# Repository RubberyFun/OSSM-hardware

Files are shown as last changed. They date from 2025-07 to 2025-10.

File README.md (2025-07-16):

# OSSM - Open Source Sex Machine

OSSM Overview Image

### [**KinkyMakers Discord Community**](https://discord.gg/wrENMKb3) 
  
Most OSSM development takes place through ideas and CAD contributions made by enthusiastic discord members, join the discussion or show off your build!  

### Check out our docs at [GitBook](https://kinky-makers.gitbook.io/)

### [**Read the Frequently Asked Questions**](FAQ.md)

## **Summary**   
**OSSM** (pronounced like "awesome") is a user friendly every day sex machine for the people.

The OSSM's primary feature is that it is a servo powered belt-driven linear rail.  
This allows for quiet, high torque operation at speeds up to 1 meter per second, as well as for software-defined stroke and depth. 

**Standard Recommended Build at a glance**
 - 32 lbs (14 kg) of force @ 20v DC
   - Up to 50 lbs (22 kg) @ 36v DC
 - 8" Stroke (20 cm) with 350mm rail

This project aims to help people curious about sex machines explore their interest.   
A second objective is optionally learning how mechanics, electronics, physics and computing are involved in your sexual pleasure.

### **Primary** Design Goals
- Compact & quiet
- Highly performant
- Moderate cost
- 3D printable
- Easily-sourced components
- Moddable
  
<p align="center">

</p>

Note: This is a _work in progress_ and we have attempted to keep compatibility with the current BOM going
forward, but it's not guaranteed.

### Is it *actually* Open Source?
    CERN Open Hardware Licence Version 2 - Strongly Reciprocal
It is one of a kind Certified, Actual, Factual, Open Source  
[](https://certification.oshwa.org/ca000057.html)

Contributions to this GitHub repository assume the same license.

## **Safety**

The safety of the OSSM is yet to be fully characterized as it is a work in progress.  
The OSSM is a framework for building your own sex machine and as such your specific combination may have risks not inherent to other builds.  
**These risks may be undocumented or undiscovered. Please see the [Hazards](Documentation/Hazards.md) file for more information.**

Use of experimental/modified code increases the level of risk.

While using the OSSM we can suggest the following hierarchy of safety, however it is up to you and your build to decide
what risks exist and how to mitigate them.

1. Have ability to move away
2. Have ability to remove the power
3. If you are in bondage, safety is responsibility of the Top

## **Building Your OSSM**
### Motor Support  
 - 57AIM30 "Gold Motor" (Standard Recommended)
 - 42AIM30 "Round Motor" (Smaller form factor, limited mounting support)
 - iHSV57 "Legacy Motor" (Pre-2024 recommended motor)

The OSSM Software is written to support closed loop servo type motors and tested on the above motors.  
Most OSSM actuator and mounting hardware is designed for NEMA23 form factor motors.  
Attempting to use a stepper or other motor is not recommended; while it may be technically possible in some cases, this usually requires custom design work and advanced-level custom code. 

### Bill Of Materials for Standard Recommended Build

### Electronics  

 - Motor 
   - 57AIM30 ["Gold Motor"](https://www.researchanddesire.com/products/ossm-motor-gold-motor)
     - **Important note:** In order to operate with OSSM Software, motors must receive programming to set their "steps per revolution" to 800.
     - Motors from R+D are pre-programmed for OSSM. Motors from all other sources will need programming.
     - Programming requires a USB to 4 pin RS485 connector, cable for the 8 pin white motor plug, and use of the [Gold Motor Programming Tool](/Hardware/Servo%20Tools/Gold%20Motor/)
 - OSSM Reference Board, Remote, Wiring
    - [OSSM Reference PCB](https://www.researchanddesire.com/products/ossm-reference-board) or ESP32 Development Board
      - More information for board development [here](/Documentation/Board_Design.md).
    - [OSSM Remote](https://www.researchanddesire.com/products/ossm-reference-board)
    - JST-PH 2.0 4-Pin data cable and 16awg power wire
      - [Wire harness - Gold Motor](https://www.researchanddesire.com/products/ossm-wire-harness-gold-motor)
 - 20-36v DC Power Supply (5.5 x 2.1 Barrel Plug)
   - [24 volt 5 amp](https://www.researchanddesire.com/products/ossm-24v-power-supply) is recommended
   - Higher voltage, up to 36v, will provide increased force
   - USB Power Banks capable of true 100w USB PD also generally seem to operate well for a portable OSSM
     - [TESTED: ✓] INIU Power Bank P63-E1 100w (Old model: B63)
     - [TESTED: Powers down on high load] INIU B62 Power Bank 65W

### [**Printed Parts**](Printed%20Parts/) 
 - [Actuator](Printed%20Parts/Actuator/)
   - Body
   - Belt Tensioner
   - Threaded End Effector, Clamp + Nut  
 - [Remote](Printed%20Parts/Remote/)
   - Body
   - Knobs
 - [Toy Mounting](Printed%20Parts/Toy%20Mounting/)
   - Flange Base Plate with Clamping Ring (Tie-Down or Suction)
   - Double Double (Vac-U-Lock)
 - [Mounting](Printed%20Parts/Mounting/)
   - Mounting Ring (PitClamp Mini Ring)
   - Base (PitClamp Mini Base)
   - PCB Enclosure
 - [Stand](Printed%20Parts/Stand/)
   - 3030 Extrusion Base

Experimental parts pop up in the [KinkyMakers Discord](https://discord.gg/wrENMKb3) #ossm-print-testing channel.  
W.I.P. for the top rated to be merged into this repo.

### Standard Actuator Hardware
**GT2 Pulley** 

    (Qty 1) 8mm Bore, 20 Tooth, 10mm Width
**GT2 Timing Belt** 

    (Qty 1) 10mm Width, 500mm length
**MGN12H Rail + Bearing Block**

    (Qty 1)
    Minimum 250mm
    Suggested 350mm
    Maximum 550mm

Rail length = desired maximum stroke + 180mm  
Must be MGN**12H** rail.  
H is a longer bearing block than C for greater stability. 12 indicates 12mm rail width.

**Ball Bearings**

    (Qty 6) MR115-2RS 5x11x4mm 

**Fasteners**  

    (Qty 10) M3x8  Socket Cap Head Bolt 
    (Qty 2) M3x20 Socket Cap Head Bolt 
    (Qty 8) M3 Hex Nut
    (Qty 3) M5x20 Socket Cap Head Bolt
    (Qty 1) M5 Hex Nut
    (Qty 4) M5x35 Socket Cap Head Bolt 
    (Qty 4) M5 20mm Hex Coupling Nut (Or M5 Hex Nut)

 Recently, the standard thread and belt clamp recommendations have been reverted to the 'classic' design from the 24mm Clamping Thread.  
 Browse the Non-standard directory for alternative belt clamp and thread designs.  
 Some preconfigured 3mf files and renders may still show a 24mm Clamping Thread design which combines the thread and belt tensioner.  

(Alternative) 24mm Clamping Thread BOM:  
    
    (Qty 2) M3x16 Socket Cap Head Bolt
    (Qty 2) M3 Hex Nuts
    Replaces hardware above:
    (Qty 2) M3x8 Socket Cap Head Bolt
    (Qty 1) M3x20 Socket Cap Head Bolt

**Additional hardware is required for Stand, Mounting, Remote  
Detailed in their respective [Printed Parts](Printed%20Parts/) folder**

## Assembly

**Important note:** The actuator rail direction is critical for pattern accuracy and safety functions. The proper direction is with the threaded end to the right when looking at the front face of the actuator body - the "M" side of the OSSM text on the Cover.  
Outdated videos and documentation may show different directions. Your rail should extend the threaded end first when booted; if this does not match the behavior of your build you should reverse your rail's printed hardware.

  
### [**Build Instructions**](Documentation/Assembly%20Instructions.pdf)
(03.30.2025) Note: There have been recent improvements to the OSSM Standard Recommended build that are not yet reflected in this build document.  
Refer to exploded views from the Printed Parts folders for assembly of each major component.
## Build Videos

[OSSM Assembly Playlist](https://youtube.com/playlist?list=PLzSK7OAu3KNQsFo6WJGT8P28lfkD3xpps)

[OSSM Complete Assembly - Follow Along Guide](https://www.youtube.com/watch?v=9lVobSEw_Uw)

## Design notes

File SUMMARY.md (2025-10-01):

# Table of contents

- [OSSM - Open Source Sex Machine](README.md)
- [Contributor Covenant Code of Conduct](CODE_OF_CONDUCT.md)
- [Contributing to OSSM (Open Source Sex Machine)](CONTRIBUTING.md)
- [Frequently Asked Questions](FAQ.md)
- [CAD Project](<CAD Project/Readme.md>)
  - [MAIN](<CAD Project/Main/README.md>)
    - [OSSM CAD Project Release Notes](<CAD Project/MAIN/RELEASE_NOTES.md>)
    - [MAIN](<CAD Project/MAIN/README.md>)
- [Documentation](Documentation/README.md)
  - [Assembly Instructions](<Documentation/Assembly Instructions.md>)
  - [Board_Design](Documentation/Board_Design.md)
  - [New Standard Servo Motor](Documentation/Gold-Motor.md)
  - [Hazards](Documentation/Hazards.md)
  - [Safety and designing for the OSSM](<Documentation/Safety and Design Guide.md>)
- [Software](Software/README.md)
  - [OSSM Project Documentation](Software/docs/README.md)
    - [PlatformIO](Software/docs/PlatformIO.md)
    - [LED Status](Software/docs/LED_Status.md)
  - [Include Directory](Software/include/README.md)
  - [Libraries Directory](Software/lib/README.md)
    - [StrokeEngine](Software/lib/StrokeEngine/README.md)
      - [CHANGELOG](Software/lib/StrokeEngine/CHANGELOG.md)
      - [Pattern](Software/lib/StrokeEngine/Pattern.md)
      - [Examples](Software/lib/StrokeEngine/examples/README.md)
  - [Testing](Software/test/README.md)
    - [Display](Software/src/services/display.md)
      - [BLE Protocol](Software/src/services/communication/BLE_Protocol.md)
    - [Command](Software/src/command/README.md)
- [Hardware](Hardware/README.md)
  - [Mounting Options](<Hardware/OSSM Mounting/readme.md>)
    - [Deprecated - Ball Head Mount](<Hardware/OSSM Mounting/Deprecated - Ball Head Mount/readme.md>)
    - [OSSM - Basic Mount](<Hardware/OSSM Mounting/OSSM - Basic Mount/README.md>)
    - [OSSM - Extrusion Mount](<Hardware/OSSM Mounting/OSSM - Full Extrusion Mount/README.md>)
    - [Shicks 4040 mount](<Hardware/OSSM Mounting/Shicks 4040 mount/Readme.md>)
      - [Modified 4040 parts](<Hardware/OSSM Mounting/Shicks 4040 mount/aluxprofile/README.md>)
  - [PCB Files](<Hardware/PCB Files/README.md>)
    - [OSSM Remote V2](<Hardware/PCB Files/OSSM Remote V2/README.md>)
  - [Servo Tools](<Hardware/Servo Tools/README.md>)
    - [Gold Motor](<Hardware/Servo Tools/Gold Motor/readme.md>)
    - [[LEGACY] OSSM Printed Parts](<Hardware/[LEGACY] OSSM Printed Parts/README.md>)
      - [Readme](<Hardware/[LEGACY] OSSM Printed Parts/OSSM Mounting/readme.md>)
        - [Aluxprofile](<Hardware/[LEGACY] OSSM Printed Parts/OSSM Mounting/Shicks 4040 mount/aluxprofile/README.md>)
        - [Readme](<Hardware/[LEGACY] OSSM Printed Parts/OSSM Mounting/Shicks 4040 mount/Readme.md>)
        - [OSSM Full Extrusion Mount](<Hardware/[LEGACY] OSSM Printed Parts/OSSM Mounting/OSSM - Full Extrusion Mount/README.md>)
        - [OSSM Basic Mount](<Hardware/[LEGACY] OSSM Printed Parts/OSSM Mounting/OSSM - Basic Mount/README.md>)
        - [Readme](<Hardware/[LEGACY] OSSM Printed Parts/OSSM Mounting/Deprecated - Ball Head Mount/readme.md>)
      * [End Effector Options](<Hardware/[LEGACY] OSSM Printed Parts/end effector options/README.md>)
        * [24mm Threaded](<Hardware/[LEGACY] OSSM Printed Parts/end effector options/24mm threaded/README.md>)
- [Printed Parts](<Printed Parts/README.md>)
  - [Actuator](<Printed Parts/Actuator/README.md>)
  - [Mounting](<Printed Parts/Mounting/README.md>)
    - [PitClamp Mini](<Printed Parts/Mounting/PitClamp Mini/README.md>)
      - [ASSEMBLY_GUIDES](<Printed Parts/Mounting/PitClamp Mini/ASSEMBLY_GUIDES.md>)
      - [PitClamp Mini Bill Of Materials](<Printed Parts/Mounting/PitClamp Mini/BOM.md>)
      - [UPDATES](<Printed Parts/Mounting/PitClamp Mini/UPDATES.md>)
  - [OSSM - Remote](<Printed Parts/Remote/README.md>)
  - [Stand](<Printed Parts/Stand/README.md>)
  - [OSSM Mods](<Printed Parts/OSSM Mods/README.md>)
    - [PitClamp Mini Reinforced 3030 Hinges](<Printed Parts/OSSM Mods/PitClamp Mini Reinforced 3030 Hinges/README.md>)
    - [PitClamp Mini Reinforced Standard](<Printed Parts/OSSM Mods/PitClamp Mini Reinforced Standard/README.md>)
    - [Threaded Belt Clamp V2](<Printed Parts/OSSM Mods/Threaded Belt Clamp V2/README.md>)

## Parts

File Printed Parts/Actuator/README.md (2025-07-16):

# Actuator
<p align="center" >
    
</p>

## Printing
**Actuator Standard Print Settings:**  

    6 Walls
    Infill type: Cross Hatch (or gyroid) 15%
    Supports: None
 - **Filament estimate:** 200g
 - **Recommended filament:** PLA+
 - All parts are intended to print in the provided file default orientation.  

<!-- Reverted standard recommended to classic 24mm Thread
   - **Printing threaded components in other orientations will cause structural weakness**
   -->

**Printed parts:**

    (Qty 1) Body - Bottom
    (Qty 1) Body - Middle
    (Qty 1) Body - Cover
    (Qty 1) Belt Tensioner
    (Qty 1) 24mm Thread
    (Qty 1) Belt Clamp - Top
    (Qty 1) Belt Clamp - Bottom
    (Qty 2) 24mm Nut - 5 Sided

<!-- Reverted standard recommended to classic 24mm Thread
    (Qty 1) 24mm Clamping Thread - End Effector
    (Qty 1) 24mm Clamping Thread - Belt Clamp
-->

<!-- ### [Additional Documentation](3030%20Extrusion%20Base/README.md)  -->

## Bill Of Materials

### Default Actuator Hardware
**GT2 Pulley** 

    8mm Bore, 20 Tooth, 10mm Width
**GT2 Timing Belt** 

    10mm Width, 500mm length
**MGN12H Rail + Bearing Block**

    Minimum 250mm
    Suggested 350mm
    Maximum 550mm

Rail length = desired maximum stroke + 180mm  
Must be MGN**12H** rail.  
H is a longer bearing block than C for greater stability. 12 indicates 12mm rail width.

**Ball Bearings**

    (Qty 6) MR115-2RS 5x11x4mm 

**Fasteners**  

    (Qty 10) M3x8 Socket Cap Head Bolt 
    (Qty 2) M3x20 Socket Cap Head Bolt 
    (Qty 8) M3 Hex Nut
    (Qty 3) M5x20 Socket Cap Head Bolt
    (Qty 1) M5 Hex Nut
    (Qty 4) M5x35 Socket Cap Head Bolt 
    (Qty 4) M5 20mm Hex Coupling Nut (Or M5 Hex Nut)

 Recently, the standard thread and belt clamp recommendations have been reverted to the 'classic' design from the 24mm Clamping Thread.  
 Browse the Non-standard directory for alternative belt clamp and thread designs.  
 Some preconfigured 3mf files and renders may still show a 24mm Clamping Thread design which combines the thread and belt tensioner. 
 
(Alternative) 24mm Clamping Thread BOM:  
    
    (Qty 2) M3x16 Socket Cap Head Bolt
    (Qty 2) M3 Hex Nuts
    Replaces hardware above:
    (Qty 2) M3x8 Socket Cap Head Bolt
    (Qty 1) M3x20 Socket Cap Head Bolt

## Assembly


| |  |
| ---- | ---- |

(Click to enlarge)

### Belt Routing

| Tensioner | Body | Belt Clamp |
| ----- | ----- | ---- |
|  |  |  |

(Click to enlarge)

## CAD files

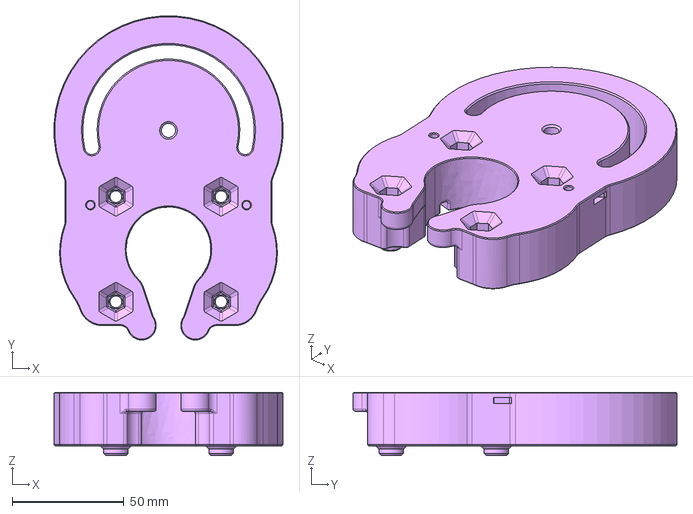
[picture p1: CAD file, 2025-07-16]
Printed Parts/Actuator/Non-standard/STEP/OSSM - Actuator - Body - Middle Pivot.stp
102.6 x 145.3 x 28.4 mm

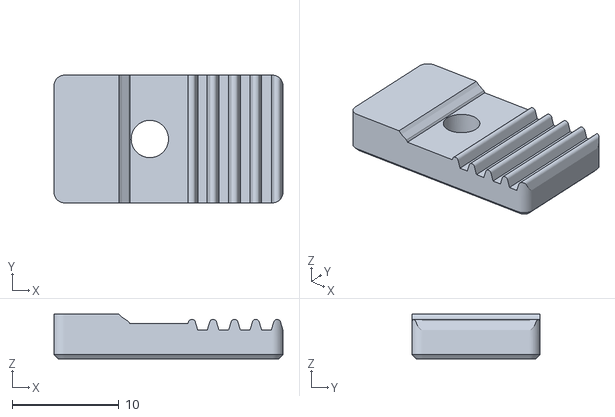
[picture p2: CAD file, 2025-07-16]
Printed Parts/Actuator/OSSM - Belt clamp - Bottom.stl
21.5 x 12.0 x 4.20

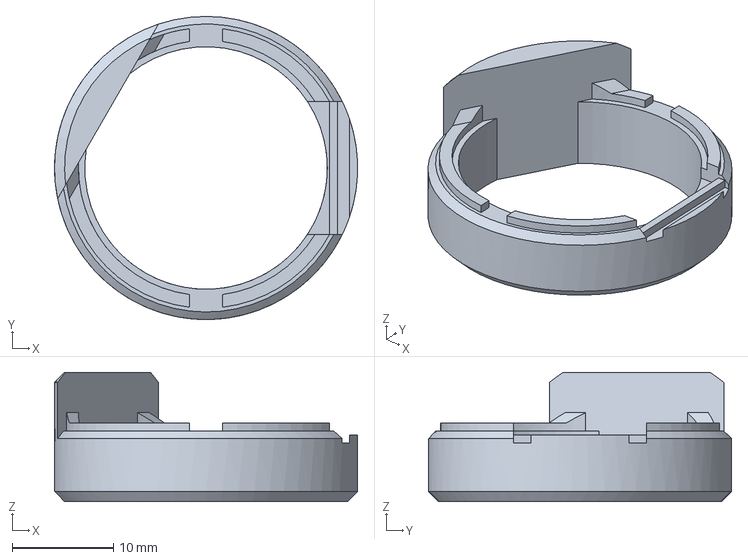
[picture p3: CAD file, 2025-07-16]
Printed Parts/Actuator/Non-standard/STEP/OSSM - 24mm Clamping Thread - Belt Clamp.stp
30.0 x 30.0 x 12.8 mm

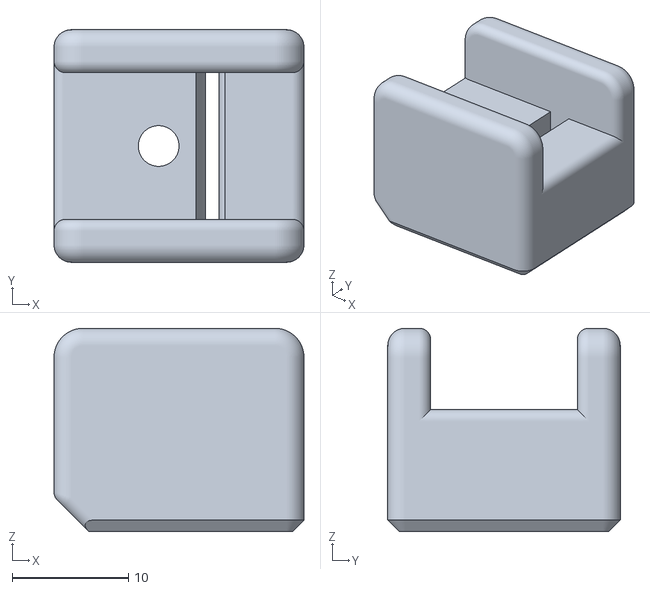
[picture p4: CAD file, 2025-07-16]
Printed Parts/Actuator/OSSM - Belt clamp - Top.stl
21.5 x 20.0 x 17.5

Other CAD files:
Printed Parts/Actuator/Non-standard/OSSM - 24mm Clamping Thread - Belt Clamp.stl

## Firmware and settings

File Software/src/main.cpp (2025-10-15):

#include "Arduino.h"
#include "OneButton.h"
#include "components/HeaderBar.h"
#include "ossm/Events.h"
#include "ossm/OSSM.h"
#include "ossm/OSSMI.h"
#include "services/board.h"
#include "services/communication/nimble.h"
#include "services/display.h"
#include "services/encoder.h"
#include "services/stepper.h"
#include "services/led.h"
#include "services/wm.h"

/*
 *  ██████╗ ███████╗███████╗███╗   ███╗
 * ██╔═══██╗██╔════╝██╔════╝████╗ ████║
 * ██║   ██║███████╗███████╗██╔████╔██║
 * ██║   ██║╚════██║╚════██║██║╚██╔╝██║
 * ╚██████╔╝███████║███████║██║ ╚═╝ ██║
 *  ╚═════╝ ╚══════╝╚══════╝╚═╝     ╚═╝
 *
 * Welcome to the open source sex machine!
 * This is a product of Kinky Makers and is licensed under the MIT license.
 *
 * Research and Desire is a financial sponsor of this project.
 *
 * But our biggest sponsor is you! If you want to support this project, please
 * contribute, fork, branch and share!
 */

OneButton button(Pins::Remote::encoderSwitch, false);

void setup() {
    /** Board setup */
    initBoard();
    yield(); // Feed watchdog

    ESP_LOGD("MAIN", "Starting OSSM");

    initWM();
    yield(); // Feed watchdog

    // Display
    initDisplay();
    yield(); // Feed watchdog

    // Initialize header bar task
    initHeaderBar();
    yield(); // Feed watchdog

    ossm = new OSSM(display, encoder, stepper);
    ossmInterface = ossm;
    yield(); // Feed watchdog

    // Initialize LED for BLE and machine status indication
    ESP_LOGI("MAIN", "LED initialized for BLE and machine status indication");
    updateLEDForMachineStatus();  // Set initial LED state
    yield(); // Feed watchdog

    // // link functions to be called on events.
    button.attachClick([]() { ossm->sm->process_event(ButtonPress{}); });
    button.attachDoubleClick([]() { ossm->sm->process_event(DoublePress{}); });
    button.attachLongPressStart([]() { ossm->sm->process_event(LongPress{}); });

    xTaskCreatePinnedToCore(
        [](void *pvParameters) {
            while (true) {
                button.tick();
                vTaskDelay(25 / portTICK_PERIOD_MS);
            }
        },
        "buttonTask", 4 * configMINIMAL_STACK_SIZE, nullptr,
        configMAX_PRIORITIES - 1, nullptr, 0);

    // Initialize NimBLE only when in menu.idle state
    xTaskCreatePinnedToCore(
        [](void *pvParameters) {
            bool initialized = false;
            while (true) {
                if ((ossm->sm->is("menu.idle"_s) ||
                     ossm->sm->is("error.idle"_s)) &&
                    !initialized) {
                    ESP_LOGD("MAIN", "Initializing NimBLE");
                    initNimble();
                    initialized = true;
                    vTaskDelete(nullptr);
                }
                vTaskDelay(pdMS_TO_TICKS(100));
            }
        },
        "initNimbleTask", 6 * configMINIMAL_STACK_SIZE, nullptr,
        configMAX_PRIORITIES - 1, nullptr, 0);
        
    ESP_LOGI("MAIN", "Setup completed successfully");
};

void loop() { vTaskDelete(nullptr); };

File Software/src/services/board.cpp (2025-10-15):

#include "board.h"

bool USE_SPEED_KNOB_AS_LIMIT = true;

void initBoard() {
    Serial.begin(115200);
    ESP_LOGI("BOARD", "Board initialization starting...");

    pinMode(Pins::Remote::encoderSwitch,
            INPUT_PULLDOWN);  // Rotary Encoder Pushbutton

    pinMode(Pins::Driver::motorEnablePin, OUTPUT);
    pinMode(Pins::Wifi::resetPin, INPUT_PULLDOWN);
    // TODO: Remove wifi toggle pin
    //    pinMode(Pins::Wifi::controlTogglePin, LOCAL_CONTROLLER); // choose
    //    between WIFI_CONTROLLER and LOCAL_CONTROLLER
    // Set analog pots (control knobs)
    pinMode(Pins::Remote::speedPotPin, INPUT);
    adcAttachPin(Pins::Remote::speedPotPin);

    analogReadResolution(12);
    analogSetAttenuation(ADC_11db);  // allows us to read almost full 3.3V range
    
    ESP_LOGI("BOARD", "Initializing stepper...");
    initStepper();
    yield(); // Feed watchdog after stepper init
    
    ESP_LOGI("BOARD", "Initializing encoder...");
    initEncoder();
    yield(); // Feed watchdog after encoder init
    
    ESP_LOGI("BOARD", "Initializing LED...");
    initLED();
    yield(); // Feed watchdog after LED init
    
    ESP_LOGI("BOARD", "Board initialization completed successfully");
}

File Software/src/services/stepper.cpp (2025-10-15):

#include "stepper.h"

FastAccelStepperEngine stepperEngine = FastAccelStepperEngine();
FastAccelStepper *stepper = nullptr;
class StrokeEngine Stroker;

void initStepper() {
    stepperEngine.init();
    stepper = stepperEngine.stepperConnectToPin(Pins::Driver::motorStepPin);
    if (stepper) {
        stepper->setDirectionPin(Pins::Driver::motorDirectionPin, false);
        stepper->setEnablePin(Pins::Driver::motorEnablePin, true);
        stepper->setAutoEnable(false);
    }

    // disable motor briefly in case we are against a hard stop.
    digitalWrite(Pins::Driver::motorEnablePin, HIGH);
    
    // Feed watchdog during long delay to prevent timeout
    for (int i = 0; i < 60; i++) {
        vTaskDelay(pdMS_TO_TICKS(10)); // 10ms * 60 = 600ms total
        yield(); // Allow other tasks to run and feed watchdog
    }
    
    digitalWrite(Pins::Driver::motorEnablePin, LOW);
    vTaskDelay(pdMS_TO_TICKS(100)); // Non-blocking delay
}

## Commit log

2025-07-16 Standard belt clamp reverted to legacy separate Belt Clamp and 24mm Thread
    [OSSM - 24mm Clamping Thread - Belt Clamp.stl, OSSM - 24mm Clamping Thread - Belt Clamp.stp, OSSM - Belt clamp - Bottom.stl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]
2025-07-16 Include missing STP for Body - Middle Pivot
    [OSSM - Actuator - Body - Middle Pivot.stp]
2025-10-15 Alter watchdog keepalive style to see if user bootloop issue is addressed
    [OSSM.cpp, board.cpp, led.cpp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]
